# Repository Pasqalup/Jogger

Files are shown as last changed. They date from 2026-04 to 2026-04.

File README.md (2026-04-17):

# RP2040 powered CNC Jog Controller
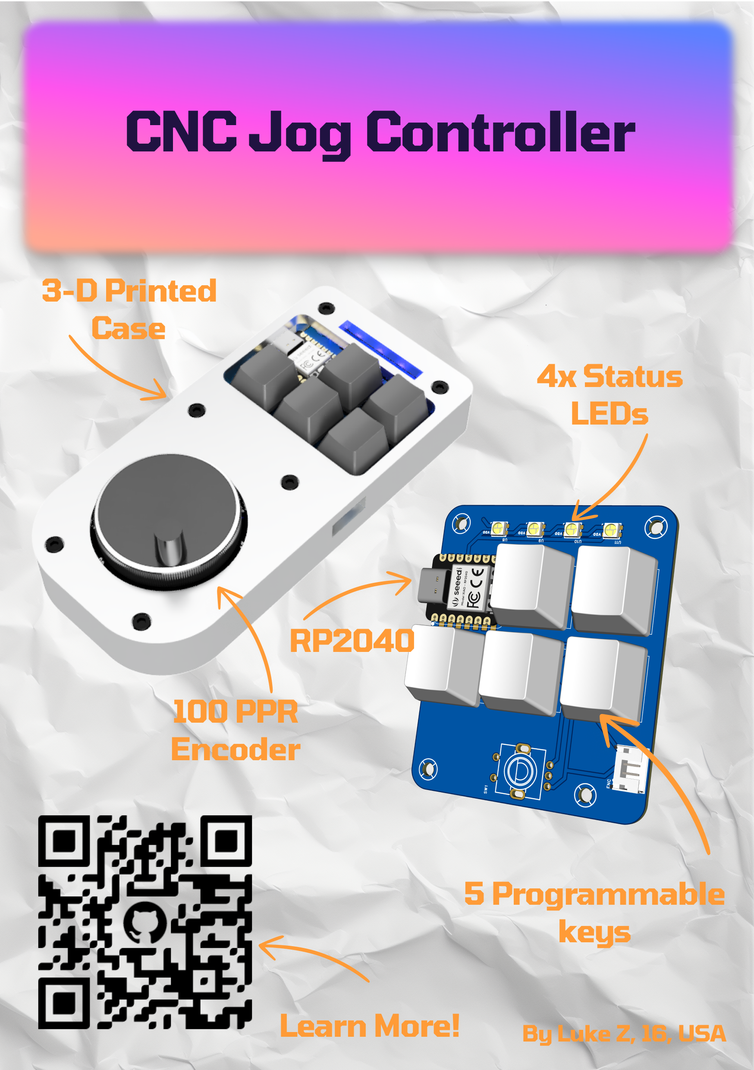
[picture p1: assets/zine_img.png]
zine page

## What is this?
This is a custom jog controller I made used to manually move CNC machines with a handheld encoder
## Why did I make this?
I use a CNC machine often to manufacture parts out of alumium and other metals, and I find it tedious to set up work coordinates and probing by clicking buttons on my screen with a trackpad.   
I designed this as an easier alternative. This will remove the need for me to look back and forth between machine and computer as I can just hold this controller by my machine. The large rotary encoder also allows for easy input.
## How to use it?
Look for hardware directions [here](pcb/) and software instructions [here](code/)
### Currently Compatible with:
- CNCjs

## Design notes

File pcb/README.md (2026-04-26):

# PCB
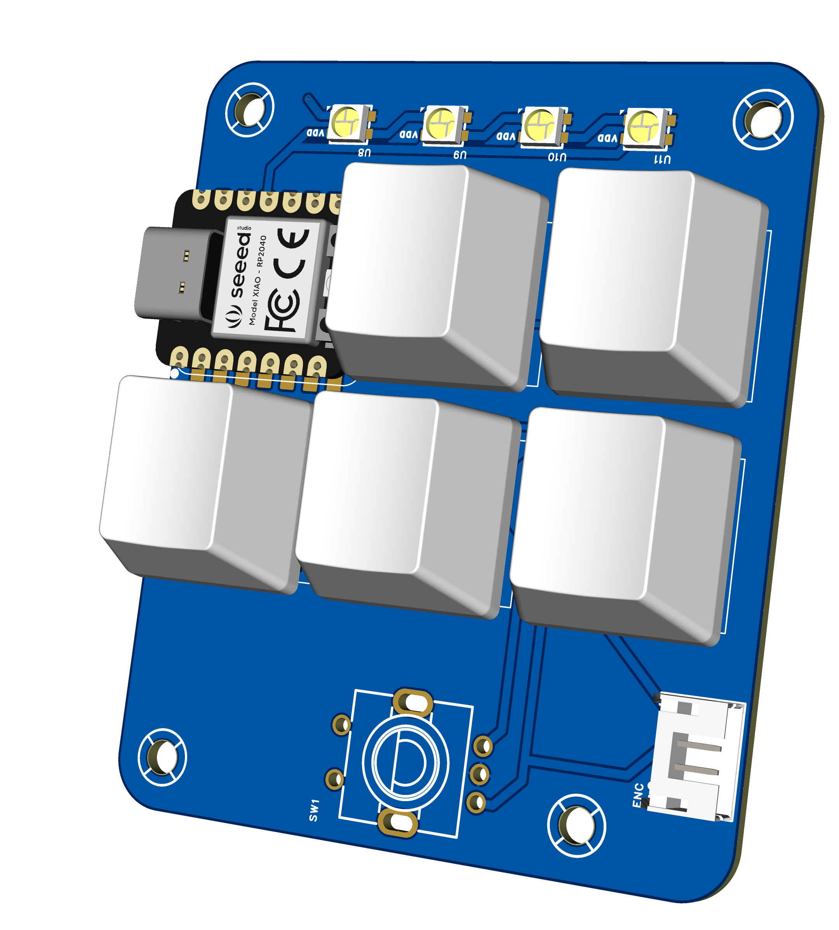
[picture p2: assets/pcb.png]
pcb


## BOM
| Part Name | Qty | Primary Link | Secondary Link | Unit Price |
|---|-----|---|---|---|
| JST connector | 1 | https://www.lcsc.com/product-detail/C157926.html | | $0.0556 |
| 100PPR Rotary Encoder | 1 | https://www.aliexpress.us/item/3256804251537752.html | | $10-15 |
| XIAO RP2040 | 1 | https://www.seeedstudio.com/XIAO-RP2040-v1-0-p-5026.html | | $3.99 |
| CHERRY MX Keyboard Switches | 5 | [https://www.lcsc.com/product-detail/CPG151101D01.html](https://www.lcsc.com/product-detail/C49234238.html) | https://www.aliexpress.us/item/3256806811817309.html | $0.1016 |
| SK6812-mini LEDs | 4 | https://www.lcsc.com/product-detail/C2886570.html | | $0.0953 |
| Cherry MX Key Caps | 5 | Your Choice! | https://www.aliexpress.us/item/3256802719703092.html | |

You may also need **JST PH** cables to connect the PCB to the encoder. If you don't have them, you can either solder wires directly to the PCB without the connector, buy [premade cables](https://www.aliexpress.us/item/3256801422042633.html) (PH 2.0mm 10CM 4P), or [crimp your own](https://www.aliexpress.us/item/3256807505634549.html) (PH 2.0)
## Assembly
1. Solder SMD LEDs
2. Solder Key switches
3. Solder XIAO RP2040 with pin headers
4. Solder JST-PH 4P connector (If you're using it)
# Schematic
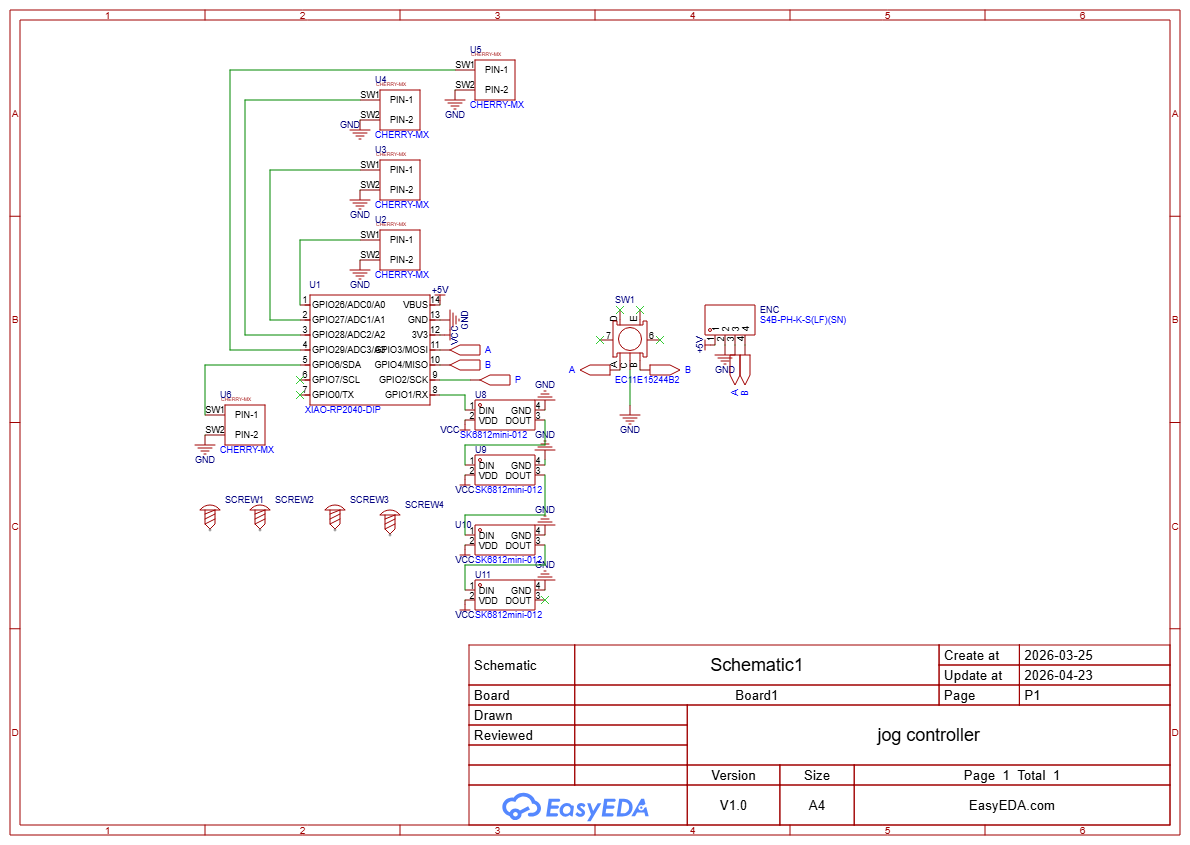
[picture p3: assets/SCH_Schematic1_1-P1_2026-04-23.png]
schematic


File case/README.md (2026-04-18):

# Case
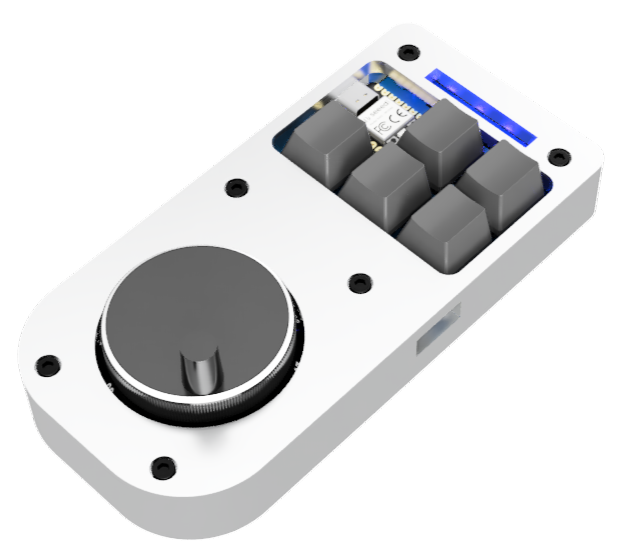
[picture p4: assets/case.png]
case

## Hardware
To assemble the case, you need:    
- 6x M3x14 socket head bolts
## Manufacturing
### 3D printing
The easiest and most accessible way is to 3D print the case.    
- Print [case top](./case%20top%20v4.step) and [case bottom](./case%20bottom%20v2.step)    

Most default print settings with PLA or PETG should be fine.    
### CNC Machining
If you have a CNC machine and want to make your case out of aluminum, I have CAM toolpaths set up for the case models. Adjust tooling and parameters to fit your machine.

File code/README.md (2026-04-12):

# Code
## For PCB
Look in [rp2040/](rp2040/)
## For GCode Sender Device
Look in [cncjs-pendant/](cncjs-pendant/)

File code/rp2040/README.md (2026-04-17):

# Controller Code
## Setup
1. Follow [this guide](https://learn.adafruit.com/adafruit-feather-rp2040-pico/arduino-ide-setup) from Adafruit to install the RP2040 into Arduino IDE
2. Select XIAO RP2040
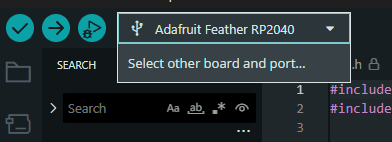
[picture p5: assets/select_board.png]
Select other board and port

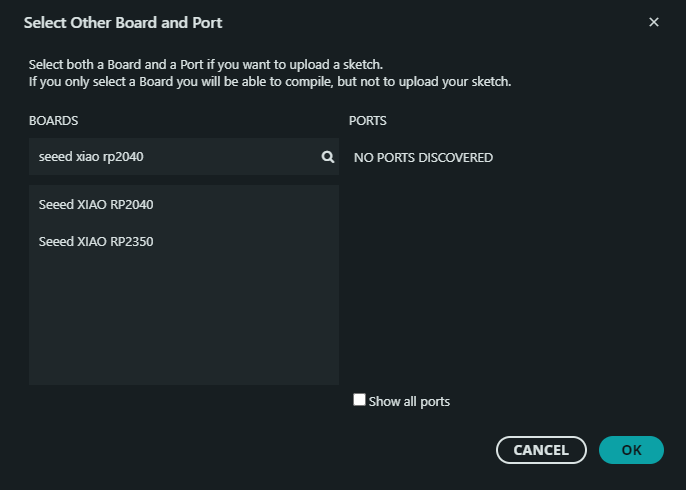
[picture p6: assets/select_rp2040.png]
Select RP2040

3. Now you can plug in your rp2040 and upload code!

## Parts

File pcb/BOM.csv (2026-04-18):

No. | Quantity | Comment | Designator | Footprint | Value | Manufacturer Part | Manufacturer | Supplier Part | Supplier | Product Link | Notes | Secondary Lihnk
1 | 1 | S4B-PH-K-S(LF)(SN) | ENC | CONN-TH_4P-P2.00_S4B-PH-K-S-LF-SN |  | S4B-PH-K-S(LF)(SN) | JST | C157926 | LCSC | https://www.lcsc.com/product-detail/C157926.html
2 | 1 | HANDWHEEL ENCODER | ENC |  |  |  |  |  | AliExpress | https://www.aliexpress.us/item/3256804251537752.html
3 | 1 | EC11E15244B2 | SW1 | SW-TH_EC11XXXXXXXX |  | EC11E15244B2 | ALPSALPINE(???????) | C470754 | LCSC | https://www.lcsc.com/product-detail/C470754.html | NOT REQUIRED
4 | 1 | XIAO-RP2040-DIP | U1 | XIAO-RP2040-DIP |  |  |  |  | Seeed Studio | https://www.seeedstudio.com/XIAO-RP2040-v1-0-p-5026.html
5 | 5 | CHERRY-MX | U2,U3,U4,U5,U6 | CHERRY-MX |  |  |  | CPG151101D01 | LCSC | https://www.lcsc.com/product-detail/CPG151101D01.html |  | https://www.aliexpress.us/item/3256806811817309.html
6 | 4 | SK6812mini-012 | U8,U9,U10,U11 | LED-SMD_4P-L3.7-W3.5-P1.75-BR-SK6812MINI |  | SK6812mini-012 | ????? | C2886570 | LCSC | https://www.lcsc.com/product-detail/C2886570.html

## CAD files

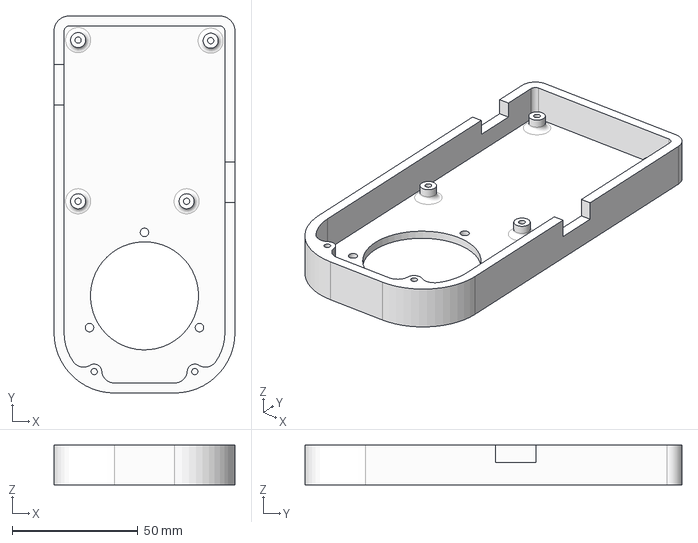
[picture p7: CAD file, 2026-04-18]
case/case bottom v2.step
72.0 x 150.0 x 15.9 mm

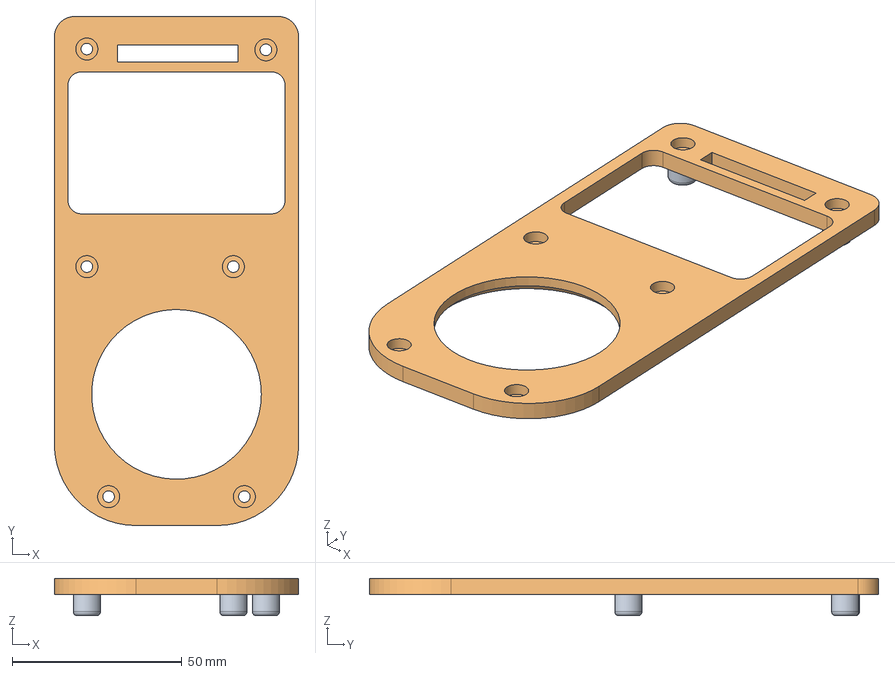
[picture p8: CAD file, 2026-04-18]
case/case top v4.step
72.0 x 150.0 x 11.0 mm

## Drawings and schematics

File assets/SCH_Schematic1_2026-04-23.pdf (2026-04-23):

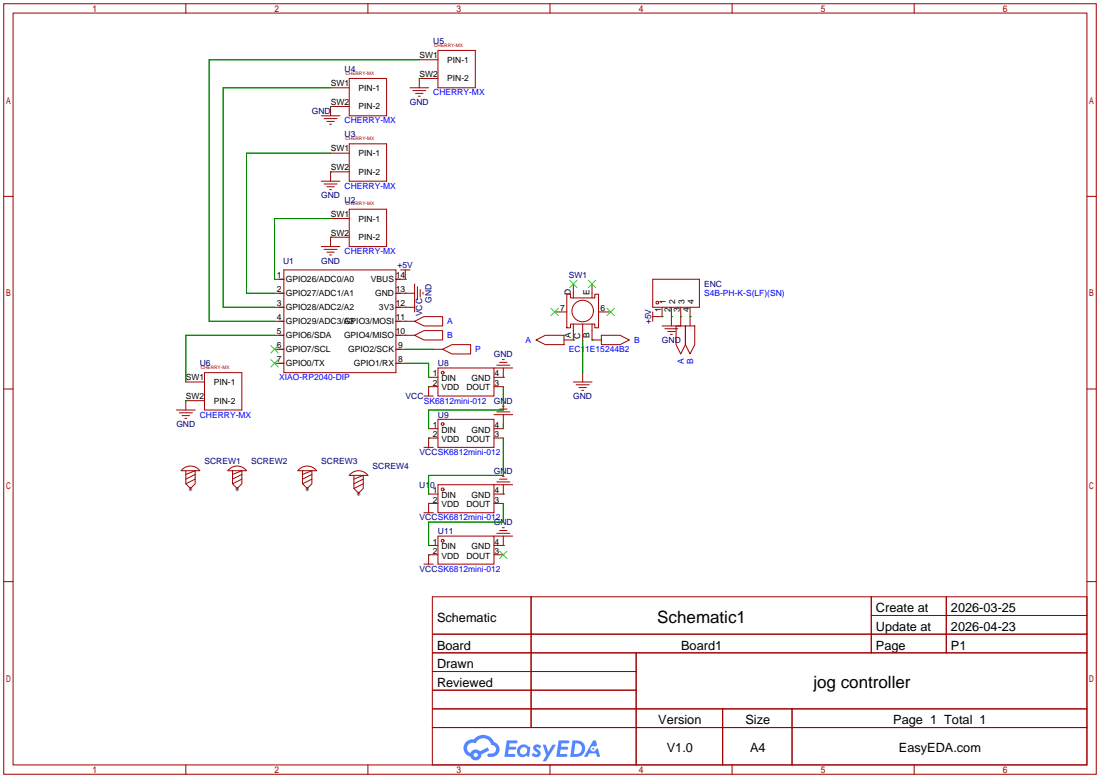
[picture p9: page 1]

Schematic | Schematic1 | Create at | 2026-03-25

Update at | 2026-04-23

Board | Board1 | Page | P1
Drawn | | jog controller
Reviewed

Version | Size | Page 1 Total 1
V1.0 | A4 | EasyEDA.com

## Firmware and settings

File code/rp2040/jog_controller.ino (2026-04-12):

#include <Adafruit_NeoPixel.h>
#include <Keyboard.h>


Adafruit_NeoPixel strip(1, 16, NEO_GRB + NEO_KHZ800);

volatile uint8_t aFlag = 0;
volatile uint8_t bFlag = 0;
volatile int32_t encoderPos = 0;
volatile uint32_t reading = 0;
volatile int32_t lastencoderPos = 0;
uint8_t buttonState = 0;
uint32_t lastEnabledTime = 0;
uint8_t lastButtonState = 0;
volatile uint8_t currentAxis = 0; // 0 for x, 1 for y, 2 for z
volatile bool enabled = 0;
#define X_BUTTON 26
#define Y_BUTTON 27
#define Z_BUTTON 28
#define EN_BUTTON 29
#define PRB_BUTTON 6
#define X_MASK (1<<0)
#define Y_MASK (1<<1)
#define Z_MASK (1<<2)
#define EN_MASK (1<<3)
#define PRB_MASK (1<<4)

/*
buttonstate
0: x
1: y
2: z
3: en button
4: probe button
*/

void setup() {
  Serial.begin(115200);
  strip.begin();
  strip.show();
  pinMode(3, INPUT_PULLUP); // encoder a
  pinMode(4, INPUT_PULLUP); // encoder b
  pinMode(X_BUTTON, INPUT_PULLUP);
  pinMode(Y_BUTTON, INPUT_PULLUP);
  pinMode(Z_BUTTON, INPUT_PULLUP);
  pinMode(EN_BUTTON, INPUT_PULLUP);
  pinMode(PRB_BUTTON, INPUT_PULLUP);
  attachInterrupt(digitalPinToInterrupt(3), encA, RISING); // attach interrupt to encoder a pin, trigger on rising edge
  attachInterrupt(digitalPinToInterrupt(4), encB, RISING);// attach interrupt to encoder b pin, trigger on rising edge

  Keyboard.begin();

}

void loop() {


  //encoder handling must happen constantly
  if(lastencoderPos != encoderPos){
    // on encoder update

    Serial.println(encoderPos);

    if(encoderPos > lastencoderPos){
      if(enabled){
        lastEnabledTime = millis(); // update activity
        Keyboard.press(KEY_F20); // forward
        Keyboard.release(KEY_F20); //release immediately
      }
      //forward
    }
    else if (encoderPos < lastencoderPos){
      if(enabled){
        lastEnabledTime = millis(); // update activity
        Keyboard.press(KEY_F19); // backward
        Keyboard.release(KEY_F19); //release immediately
      }
      //backward
    }
    lastencoderPos = encoderPos;
  }
  


  //the rest can be done periodically for debouncing
  if((millis() + 5) % 50 == 0){// 5ms after buttons are checked, release all keys to prevent sticking
    Keyboard.releaseAll(); // release all keys to prevent sticking
    //happens after encoder release so its ok
  }



  if(millis() % 50 == 0){

    // every 50 ms, check buttons and update state

    // direct read gpio without digitalRead()
    uint32_t raw_gpio = sio_hw->gpio_in;

    // parse into single byte

    // move right 26 so that 26-29 are in least 4 significant bits, mask with 0x0f for only those 4
    // move right 6 so that bit 6 is in least significant bit, mask with 0x01 for only that bit, then shift left 4 to put it in bit 5 position
    buttonState = ((raw_gpio >> 26) & 0x0F) | (((raw_gpio >> 6) & 0x01) << 4);

    // find fallling edges (0->1 because of inverted pull-up logic)
    // xor identifies all changed
    // & identifies going to high
    uint8_t changedButtons = (buttonState ^ lastButtonState) & buttonState & 0x1F; 
    lastButtonState = buttonState; // Update lastButtonState for the next iteration
    if (changedButtons & X_MASK) {
      //switch to x axis
      currentAxis = 0;
      lastEnabledTime = millis();
      Keyboard.press(KEY_F16);


    } else if (changedButtons & Y_MASK) {
      //switch to y axis
      currentAxis = 1;
      lastEnabledTime = millis();
      Keyboard.press(KEY_F17);


    } else if (changedButtons & Z_MASK) {
        //switch to z axis
        currentAxis = 2;
        lastEnabledTime = millis();
        Keyboard.press(KEY_F18);


    }
    else if (changedButtons & EN_MASK) {
      //toggle enable state
        if(enabled){
          enabled = false;
          Keyboard.press(KEY_F13); // lock
        }
        else{
          enabled = true;
          Keyboard.press(KEY_F14); // unlock
        }

    } else if (changedButtons & PRB_MASK) {


        // PRB button is pressed
        lastEnabledTime = millis();
        if (enabled) {
          Keyboard.press(KEY_F15); // probe
        }


    }
    else {
        // No buttons are pressed, release all keys
        Keyboard.releaseAll();
    }

    if (millis() - lastEnabledTime > 10000) { // 10 seconds of inactivity
      enabled = false;
      Keyboard.press(KEY_F13); // lock
    }

  }
}


void setup1(){
  // no setup on core 1
}


bool blinkon = false;

// core 1 loop for handling LED updates, runs independently of core 0 loop
void loop1(){
  if(enabled){
    //blink green to indicate enabled
    if(blinkon){
      blinkon = false;
      strip.setPixelColor(0,strip.Color(0,0,0)); 
    }
    else{
      blinkon = true;
      strip.setPixelColor(0,strip.Color(0,40,0)); 
    }
  }
  else{
    strip.setPixelColor(0,strip.Color(10,10,0)); // yellow to indicate disabled
  }
  if(currentAxis == 0){
    strip.setPixelColor(1,strip.Color(10,10,40)); // add bright blue to indicate x axis
    strip.setPixelColor(2,strip.Color(0,0,0)); // turn off y axis
    strip.setPixelColor(3,strip.Color(0,0,0)); // turn off z axis
  }
  else if(currentAxis == 1){
    strip.setPixelColor(2,strip.Color(10,10,40)); // add bright blue to indicate y axis
    strip.setPixelColor(1,strip.Color(0,0,0)); // turn off x axis
    strip.setPixelColor(3,strip.Color(0,0,0)); // turn off z axis
  }
  else if(currentAxis == 2){
    strip.setPixelColor(3,strip.Color(10,10,40)); // add bright blue to indicate z axis
    strip.setPixelColor(1,strip.Color(0,0,0)); // turn off x axis
    strip.setPixelColor(2,strip.Color(0,0,0)); // turn off y axis
  }
  strip.show();
  delay(50);
  Serial.println("LED update");
}


// interrupts for encoder pulses
void encA(){
  cli();
  reading = sio_hw->gpio_in & (1<<3 | 1<<4);
  if(reading == (uint32_t)((1<<3 | 1<<4)) && aFlag){
    // a is rising, b is active, counter clockwise rotation
    encoderPos--;
    bFlag = 0;
    aFlag = 0;
  }
  else if (reading == uint32_t(1<<3)){ //a is first rising, wait for b to rise for clockwise rotation
    bFlag = 1;
  }


  sei();
}
void encB(){
  cli();
  reading = sio_hw->gpio_in & (1<<3 | 1<<4);
  if(reading == (uint32_t)((1<<3 | 1<<4)) && bFlag){
    // b is rising, a is active, clockwise rotation
    encoderPos++;
    bFlag = 0;
    aFlag = 0;
  } else if(reading == uint32_t(1<<4)){ //b is first rising, wait for a to rise for counter-clockwise rotation
    aFlag = 1;
  }
  sei();
}

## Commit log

2026-04-18 cad source
2026-04-18 case doc
    [BOM_Board1_Schematic1_2026-04-12.csv, case bottom v2.step, case top v4.step]
2026-04-18 fix bom csv
    [BOM.csv]
2026-04-18 socketio version
2026-04-26 add gerber
2026-04-26 Update BOM with unit prices and links
    Added unit prices to the BOM for components and updated links.
